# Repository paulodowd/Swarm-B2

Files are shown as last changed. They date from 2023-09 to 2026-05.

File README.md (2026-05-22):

<p align="center">
<br>
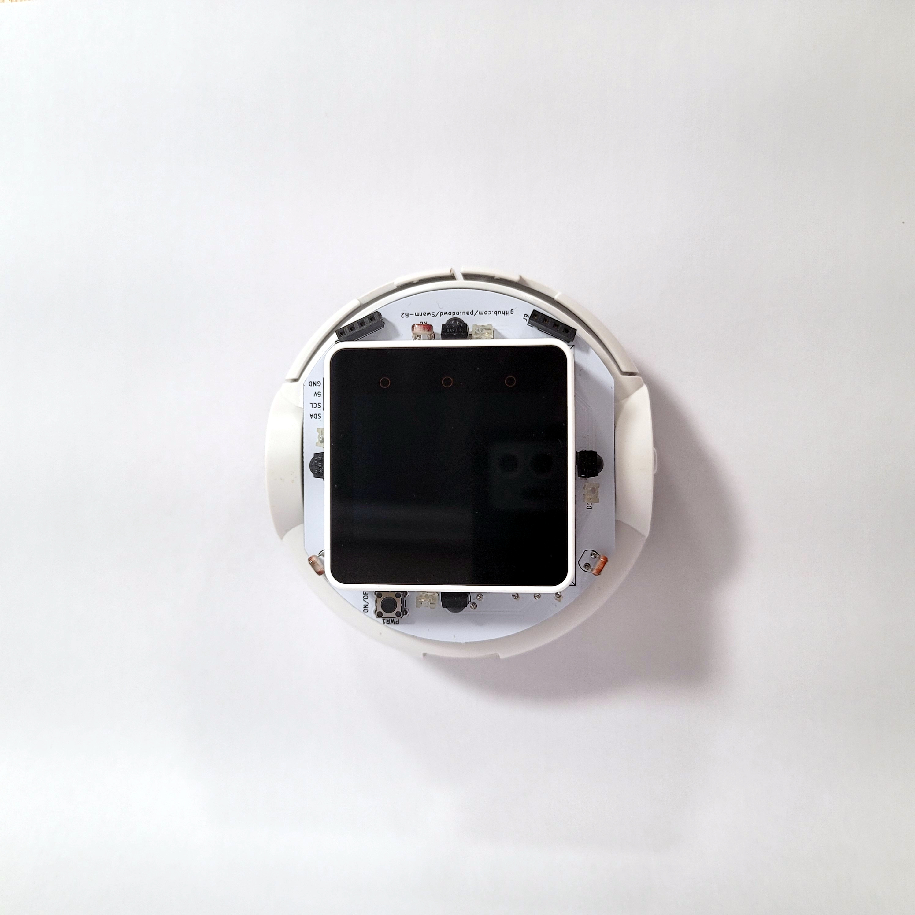
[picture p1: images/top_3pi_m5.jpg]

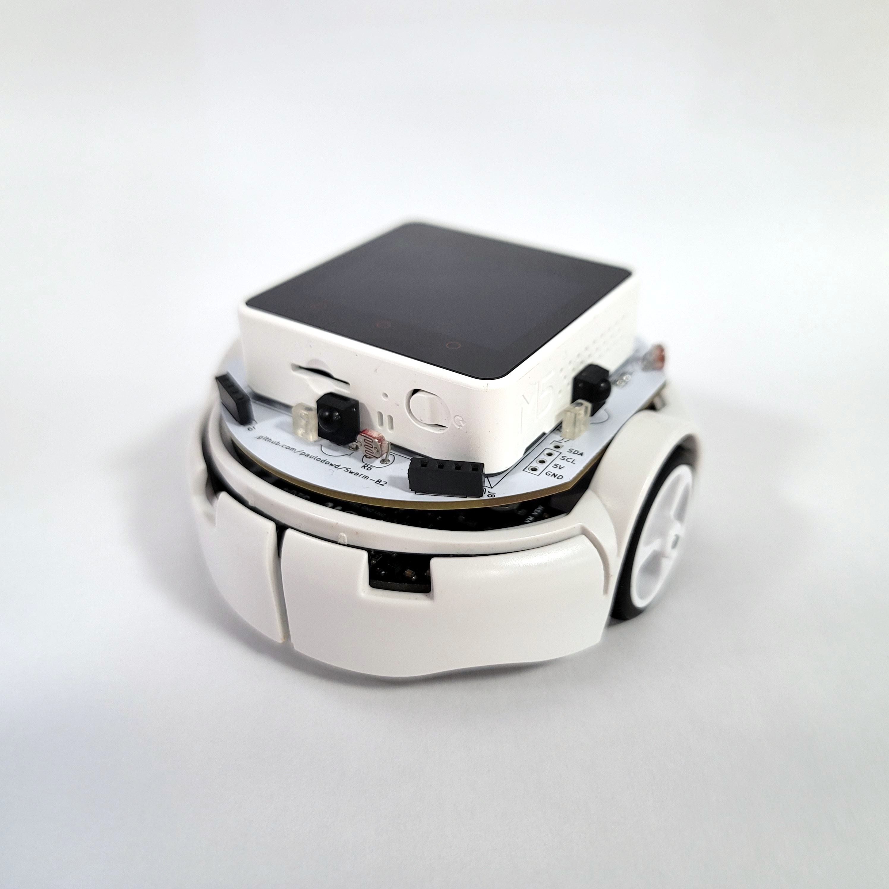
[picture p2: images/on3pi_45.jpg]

<br>
</p>

# Swarm-B2
Infra-red (IR) Communication board for Pololu 3Pi+ robots that also has a pin header to interface with an M5 Stack Core2.  This is the second major design of such a board, hence the name (S)warm (B)oard 2 - SwarmB2.  A third version is under-development with the intention to supercede this design ([SwarmB3](https://github.com/paulodowd/SwarmB3)). 

The board functions as an i2c device, so it should be relatively easy to integrate into other projects using 5v, ground, SCK and SDA connections.  The board can communicate with other SwarmB2 boards up to about 2.5m max, or down to less than a centimetre.  The firmware for the board has been written with the intention that all (or most) configuration parameters can be set at runtime, so reprogramming firmware shouldn't be necessary.

## Features
- 32 bytes per message.
- SLIP-style encoding/escaping.
- 9600 or 4800 baudrate (device dependent)
- Receive or transmit, cannot do both concurrently.
- Receiving is polled across 4 receivers.
- Transmission power set by a potentiometer (0-2.5m)
- Message framing with start delimiter and message length embedded.
- A 16 bit CRC to detect transmission errors.
- Error statistics at message level.
- Performance statitics (timings, etc).
- Bearing estimation.
- 3x LDR and 2x Sharp IR Range Finder integration on PCB.
- Reconfigurable communication strategies/priorities.
- Header pins to attach to a Pololu 3Pi+ robot.
- Header pins for an M5Stack Core2 device interfacing.

## Getting Started

The best way to get started is to download and install the example <a href="https://github.com/paulodowd/Swarm-B2/tree/main/examples/M5Visualiser">M5Visualiser</a> written for the M5Stack Core2.  This example demonstrates how to make function calls through the `SwarmB2_c` class. The class has function calls for all functionality available on the Swarm-B2, returning data types specified in the file `ircomm_i2c.h`.  

## Working with the M5Stack Core2

To get started with the M5Stack Core2, it is best to follow the manufacturers documentation to configure the Arduino IDE.  Make sure you follow the instructions for both:
- <a href="https://docs.m5stack.com/en/arduino/arduino_board">Board Management Installation</a>
- <a href="https://docs.m5stack.com/en/arduino/arduino_library">Arduino Library Installation</a>

The <a href="https://github.com/paulodowd/Swarm-B2/tree/main/examples/M5Visualiser">M5Visualiser</a> example was written against the M5Unified library - installing or using a different M5Stack library is likely to cause compilation errors for the provided example.

## Important Characteristics

### Message Size
The Swarm-B2 can receive a message of maximum length 32 bytes to transmit.  This limitation is currently defined by the Arduino i2c implementation.  The Swarm-B2 can accept a message of upto 32bytes, and it will then encode the message using a further number of bytes.   It is important to consider that when transmitting a long length message, the probability that the message will become corrupted (or similar) increases.  

### Polling
<p align="center">
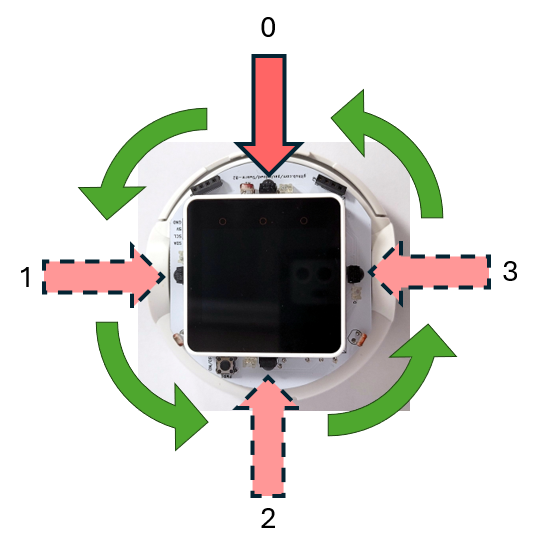
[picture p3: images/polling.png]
  
</p>
The Swarm-B2 board can only read one receiver at a time. The board is configured by default to switch which receiver is enabled as soon as one message is successfully received.  The board is also configured by default to switch receiver if it detects no activity.  Otherwise, the board is configured by default to listen for a period of time before switching receiver. 

### Transmitting
The Swarm-B2 must disable receiving to be able to transmit, otherwise it will immediately receive it's own transmission.  Therefore, the board is configured to periodically transmit messages, and in the interval period poll the receivers to receive messages.  

### Transmitting Power
The power of the IR LEDs which transmit messages can be varied via the blue potentiometer on the back of the Swarm-B2 circuit board.  The blue potentiometer has a small silver dot: rotating the white arrow indicator to point at this silver dot will produce maximum power, or maximum range of transmission.  Swarm-B2 can transmit upto 3m distance.  However, this is not very useful in a swarm/multi-robot context.  If the transmit power is set high, it is likely that the environment will become saturated with IR emissions, effectively blocking transmissions between all other robots.  The recommended position for the potentiometer is indicated in the below image with a pink dot.  This position sets the communication distance to approximately 20cm, or two robot-body lengths.

<p align="center">
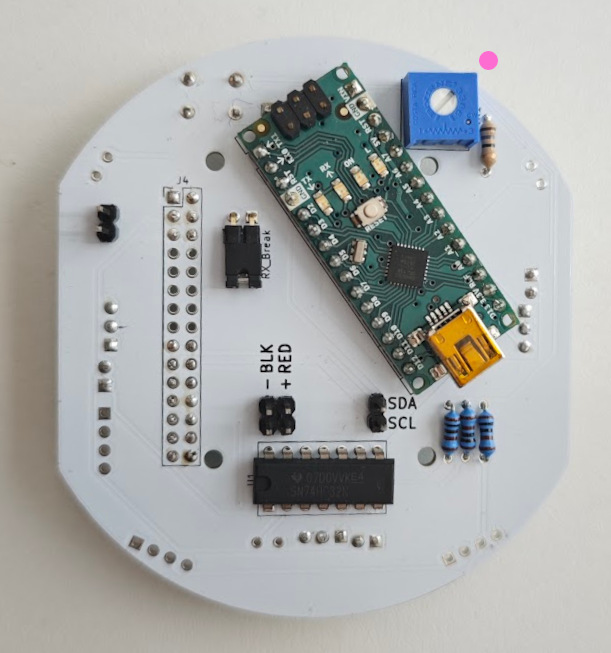
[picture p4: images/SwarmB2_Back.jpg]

</p>

### Other Configurations
It is possible to change the Swarm-B2 configuration via i2c transactions.  For example, it is possible to setup a Swarm-B2 to only transmit continously.  Or, it is possible to setup the Swarm-B2 to only receive on 1 receiver continuously.  

## FAQ

## Using the Swarm-B2 board in other Projects
This IR communication board can be used as a general purpose communication board.  The firmware on this github page is written as an i2c slave device with address `0x11`.  It should be possible to use the IR Communication board in it's current design and format with any other device that can operate the I2C protocol.  To do so, you simply need to connect the `5v`, `GND`, `SCL` and `SDA` pins appropriately to your operating device.  These physical pins are labelled on the underside of the circuit board as `+RED` (5v), `-BLK` (GND), `SDA` and `SCL`, or as `5V`, `GND`, `SCL`, `SDA` on the  topside of the circuit board.

## Fabrication, Gerber files
Navigate to folder `pcb` to find the last known gerber files sent for manufacturing, `Gerbers.zip`.  

## Schematic
The schematic of the communication board is available in picture format in the `images` folder and within the pcb folder as KiCad files.


## Interesting Information

IR communication is implemented using the standard Serial (hardware UART) functionality common to Arduino (e.g. `Serial.print()`), and so the IR circuit is electronically connected to  the Arduino TX and RX pins.  The detection (receiving) circuit uses a Demodulator chip that is tuned for a carrier frequency of 38.4Khz or 57.6Khz (more details below).  Therefore, the Arduino Nano generates a 38Khz or 58Khz signal via an internal timer interrupt to provide the transmitting carrier, output on digital pin 4.  

The carrier signal is combined electronically with the TX pin state through an OR gate (74xx32). The logic (OR) of this operation is defined by the gates sinking the current through the tranmitting IR LEDs.  Therefore, the LEDs are not driven by the 74xx32 (or the Arduino Nano, to be clear), and are considered active low.  A nice unintended side effect of this is that when TX is inactive (LOW, not transmitting), the 74xx32 output is HIGH despite the continued 38Khz signal generation - which means the IR LEDs are off and not saturating the environment.

In this circuit design, a single gate is used to sink current.  It might be important to note that the <a href="https://www.ti.com/lit/ds/symlink/sn54hc32-sp.pdf">datasheet</a> for the logic gates specifies a max current sink of 50ma through ground - and here we are potentially sinking upto 200ma from the 4 IR LEDs.    So far, I've not seen any significant changes to performance and this may be because I am not sinking current continuously, instead intermitently at 38Khz. All 4 OR gates within the 74xx32 are ganged, but the internal ground connection may still be a limitation. In either case, I haven't yet seen any problems or difference in performance.  It might be unwise to active the IR LEDs continuously (i.e. not modulated).

### Important Considerations

- **IR Demodulator:** I tried a few IR demodulator chips and they are not all created equally.  In particular, those designed to receive bursts of transmission appear poorly suited.  When using ones for burst transmission, I observed that I had to wave the transmitter or receiver around to get a successful transmission (perhaps some inner circuitry reaches a saturation?).  Instead it is better to use those designed for continuous transmission. The Vishay **TSDP34138** (<a href="https://www.farnell.com/datasheets/2245004.pdf">datasheet</a>) seems to fit this and works well / reliably.  The datasheet specifies upto 4800 baud for a 38.4Khz carrier frequency.  If you want to reproduce this board, I recommend you use the same device, or be ready for some trials of different devices.
- **Self-Receiving:** I did have an issue of a single board receiving it's own IR transmissions, and not being able to receive transmission from neighbours.  I believe this is because the UART implementation (on the Atmega328 at least) operates send (TX) and receive (RX) independently.  When using IR light, this means it will detect it's own transmission. After attempting a lot of different solutions, it was as simple as disabling the RX functionality of the UART by a register operation.  I'm glad this was available!  You can review the details of this on page 171 of the Atmega328 datasheet (<a href="https://ww1.microchip.com/downloads/en/DeviceDoc/Atmel-7810-Automotive-Microcontrollers-ATmega328P_Datasheet.pdf">here</a>).  
- **Programming the Arduino Nano:** It is important to note that the programming of the Arduino Nano will most often fail if the IR Demodulator is electronically connected.  Therefore, the circuit design has a jumper (labelled, "RX Break") intended for a connecting removable sleeve, to allow the connection to be broken for programming.  Importantly, no IR messages can be received if this jumper is not closed with the sleeve.  
- **Buffer Sizes:** The main limitation on the size of a string that can be sent over IR is actually the number of bytes that can be transferred on the I2C bus.  I think this is dependent on the Arduino Wire library and could be modifed. Or, strings to transmit could be broken into parts to transfer over I2C.  A second consideration is that the Arduino UART device has a buffer of 64 bytes.  For simplicity, the software current has buffers of 32 bytes.

## Notes on Using a M5Stack Core2

- The docs for the M5Stack Core2 are at this <a href="https://docs.m5stack.com/en/core/core2">link</a>.
- Follow the guides at <a href="https://docs.m5stack.com/en/arduino/arduino_ide">this link</a> to setup the Arduino IDE.

## Links and resources I have found useful
- Example code and discussion for different CRC algorithms: <a href="https://www.sunshine2k.de/articles/coding/crc/understanding_crc.html">link</a>
- Interesting Arduino forum post debugging CRC: <a href="https://forum.arduino.cc/t/crc-8-i2c-cyclic-redundancy-check/644812/4">link</a>
- Microchip Application Note with CRC: <a href="https://ww1.microchip.com/downloads/en/AppNotes/00730a.pdf">link</a>
- Discussion on CRC and data length: <a href="https://stackoverflow.com/questions/2321676/data-length-vs-crc-length">link</a>
- Some information on UART Baudrates: <a href="https://lucidar.me/en/serialib/most-used-baud-rates-table/">link</a>
- Discussion on start/stop bit and errors with UART: <a href="https://electronics.stackexchange.com/questions/91450/what-exactly-is-the-start-bit-error-in-uart">link</a>
- Disucssion on catching frame data overrun in UART: <a href="https://forum.arduino.cc/t/rs232-uart-frame-data-overrun-error-handling/193266/12">link</a>
- Table of ASCII values: <a href="https://www.ascii-code.com/">link</a>

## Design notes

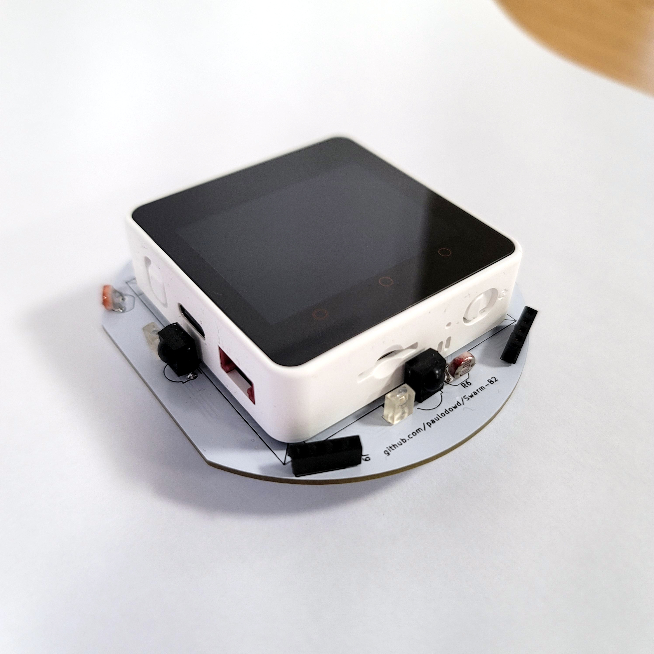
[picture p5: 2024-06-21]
images/top45_withM5.jpg

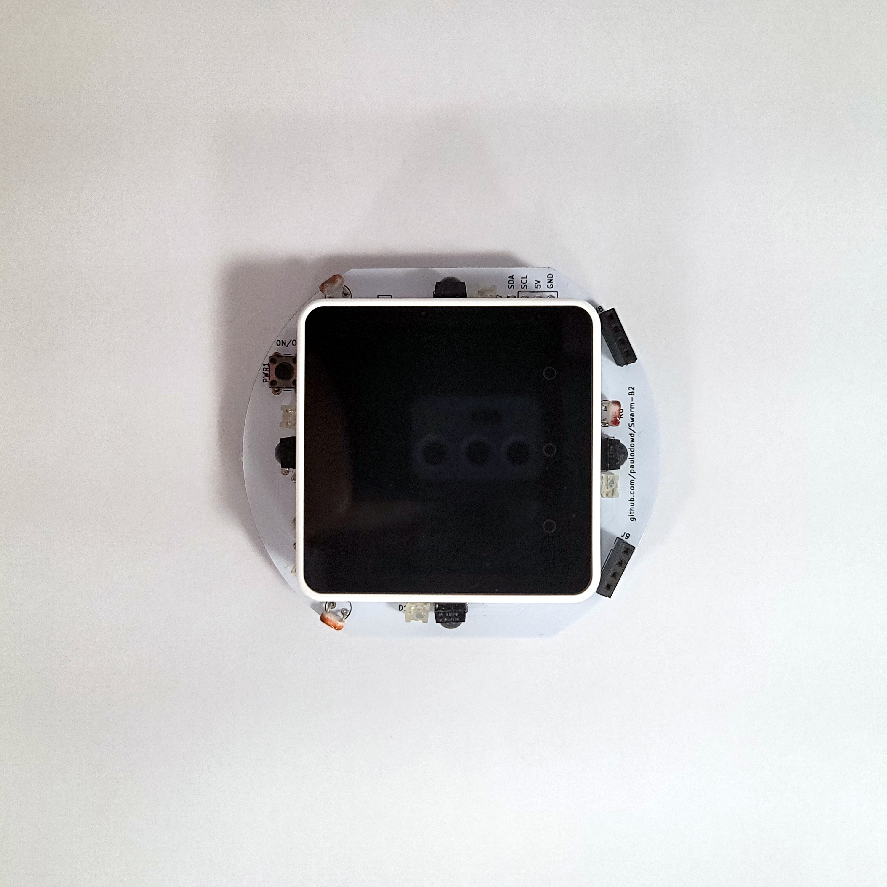
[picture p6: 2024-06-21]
images/top.jpg

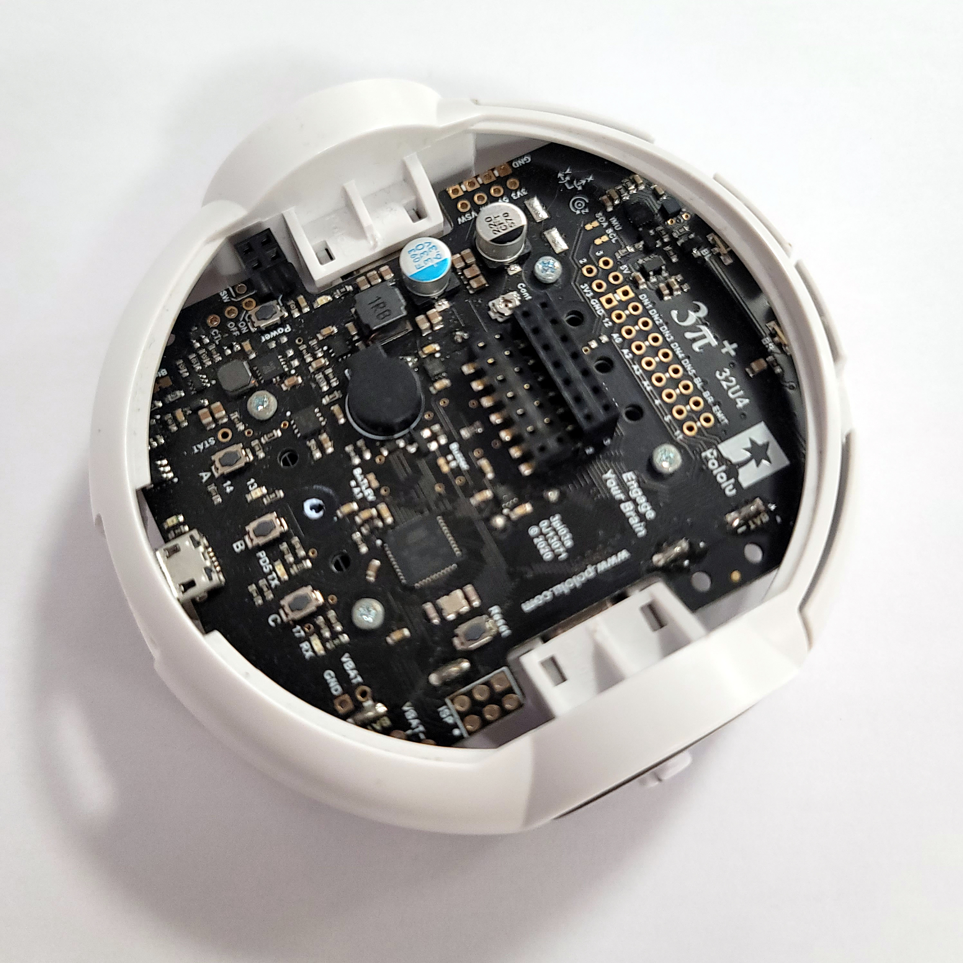
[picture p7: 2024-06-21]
images/top_3pi_modded.jpg

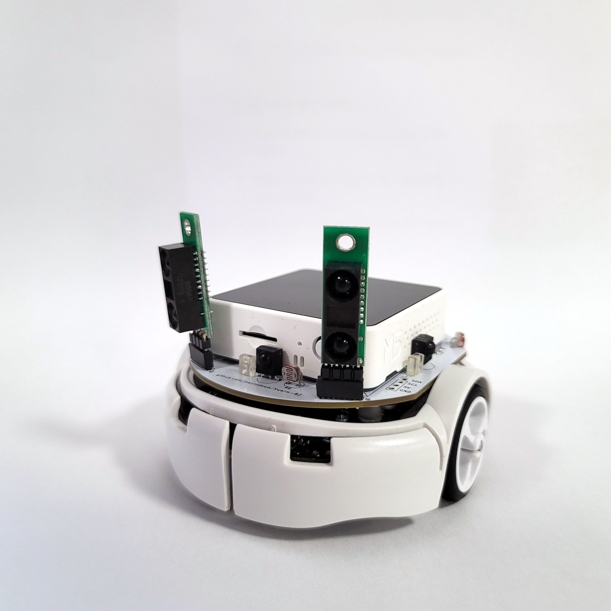
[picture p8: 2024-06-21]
images/on3pi_withProx.jpg

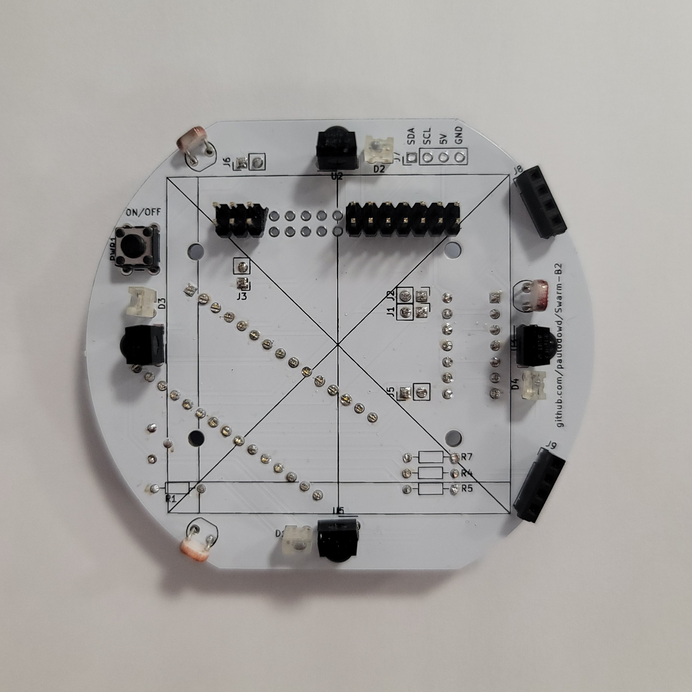
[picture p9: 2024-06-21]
images/ircomm_top.jpg

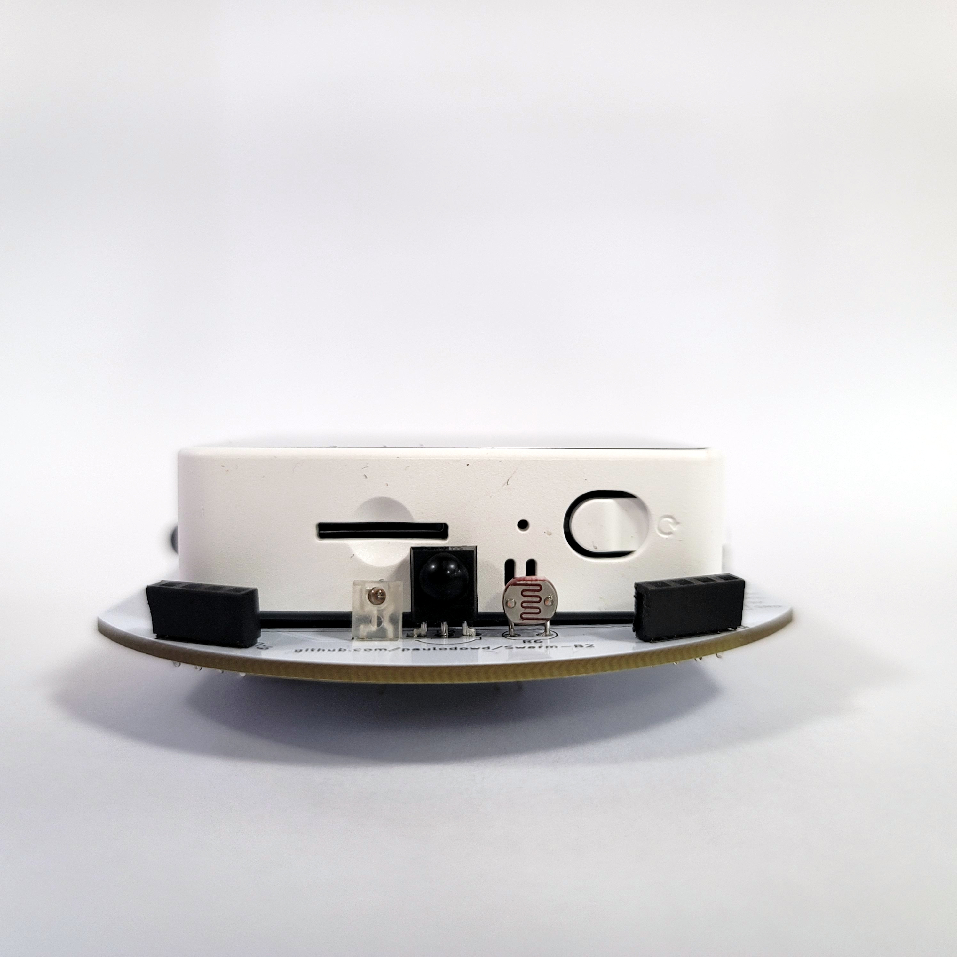
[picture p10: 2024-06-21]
images/ircomm_side_withM5.jpg

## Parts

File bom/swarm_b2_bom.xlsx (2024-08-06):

Component | Description
D1,D2,D3,D4 | IR LED, 945nm, side looking, 50 degrees emission angle
J1, J2, J5, J6 | 2 pin male header 2.54mm pitch, vertical, to Pololu 3Pi+
J3 | 2 pin male header at right angle 2.54mm pitch, for Rx_Break
J8, J9 | 4 pin female socket
J4 | M5Stack Core2 header
U1 | SN74HC32N Quad OR gate, combines UART with IR carrier signal | https://uk.farnell.com/texas-instruments/sn74hc32n/ic-quad-2-input-or-74hc32-dip14/dp/3120475 |  | 50
U2, U3, U4, U5 | TSDP34138 IR Demodulator | https://uk.farnell.com/vishay/tsdp34138/ir-receiver-35m-0-15mw-m2-side/dp/2565310 | 105 | 26.25 | 66.75
PWR1 | Mini push button 5mm
R2, R3, R6 | LDR, 5mm, 5-10k light resistance (0.5M dark resistance?).
R1 | 18R Resistor, current limiting for IR LEDs
R4, R5, R7 | 1K Resitors, potential divider for LDRs
VR1 | 1K variable resistor
A1 | Arduino Nano | https://uk.rs-online.com/web/p/arduino/6961667?searchId=df16a1f3-1ee1-491f-a64f-628fe71fe9df&gb=s |  | 58
n/a | Jumper (to connect Rx_Break)
 |  |  | 57

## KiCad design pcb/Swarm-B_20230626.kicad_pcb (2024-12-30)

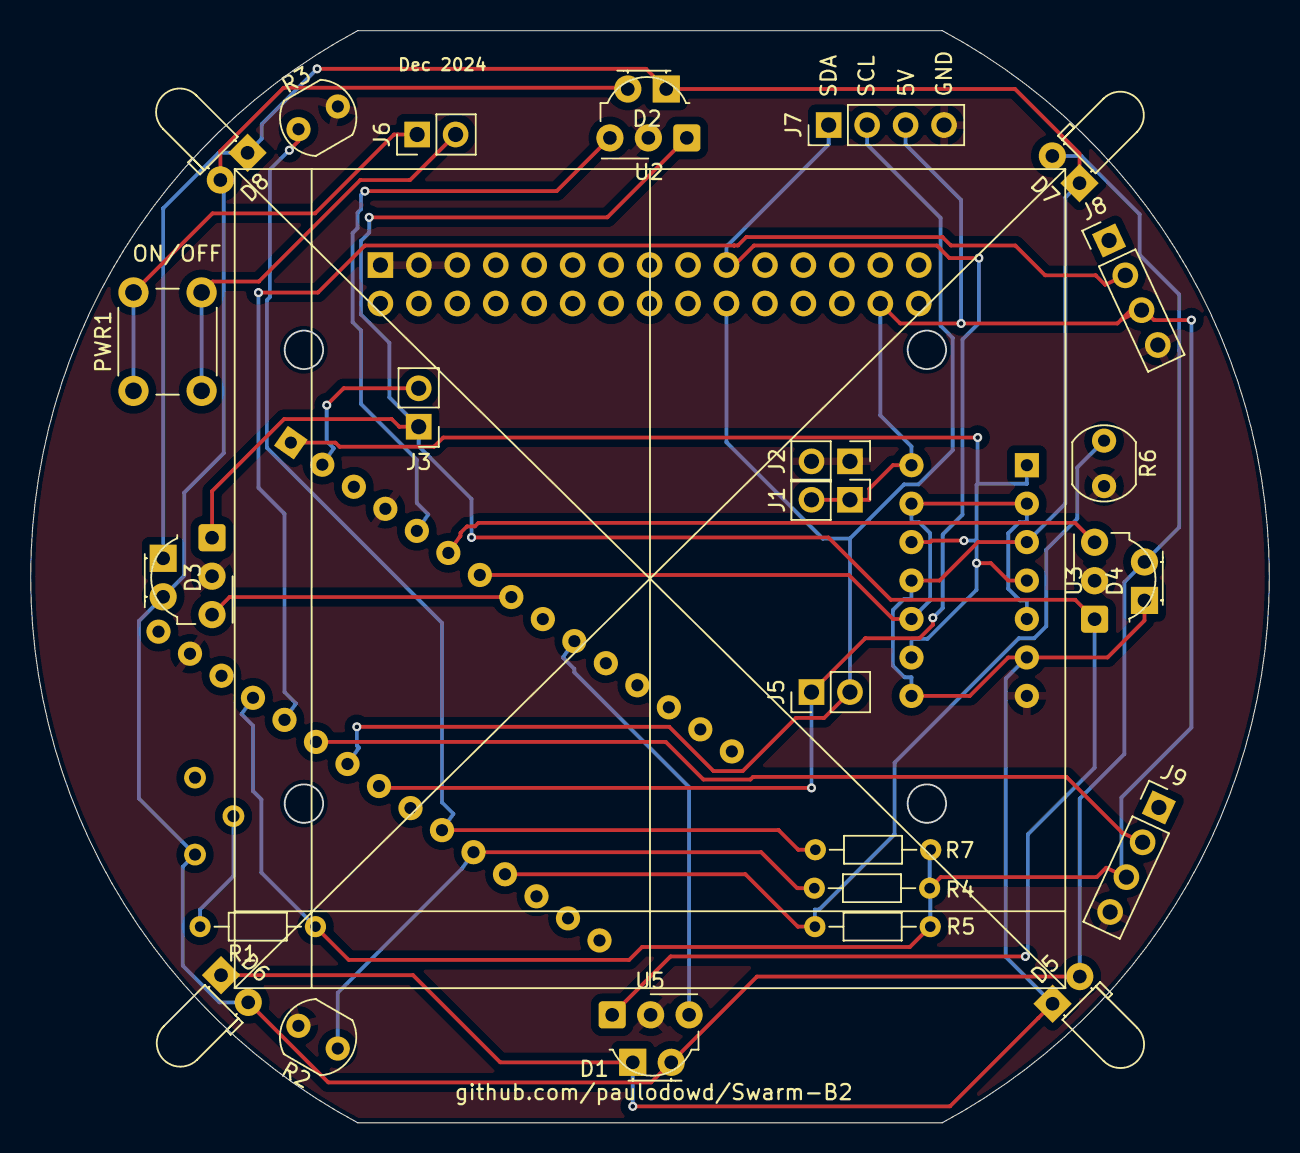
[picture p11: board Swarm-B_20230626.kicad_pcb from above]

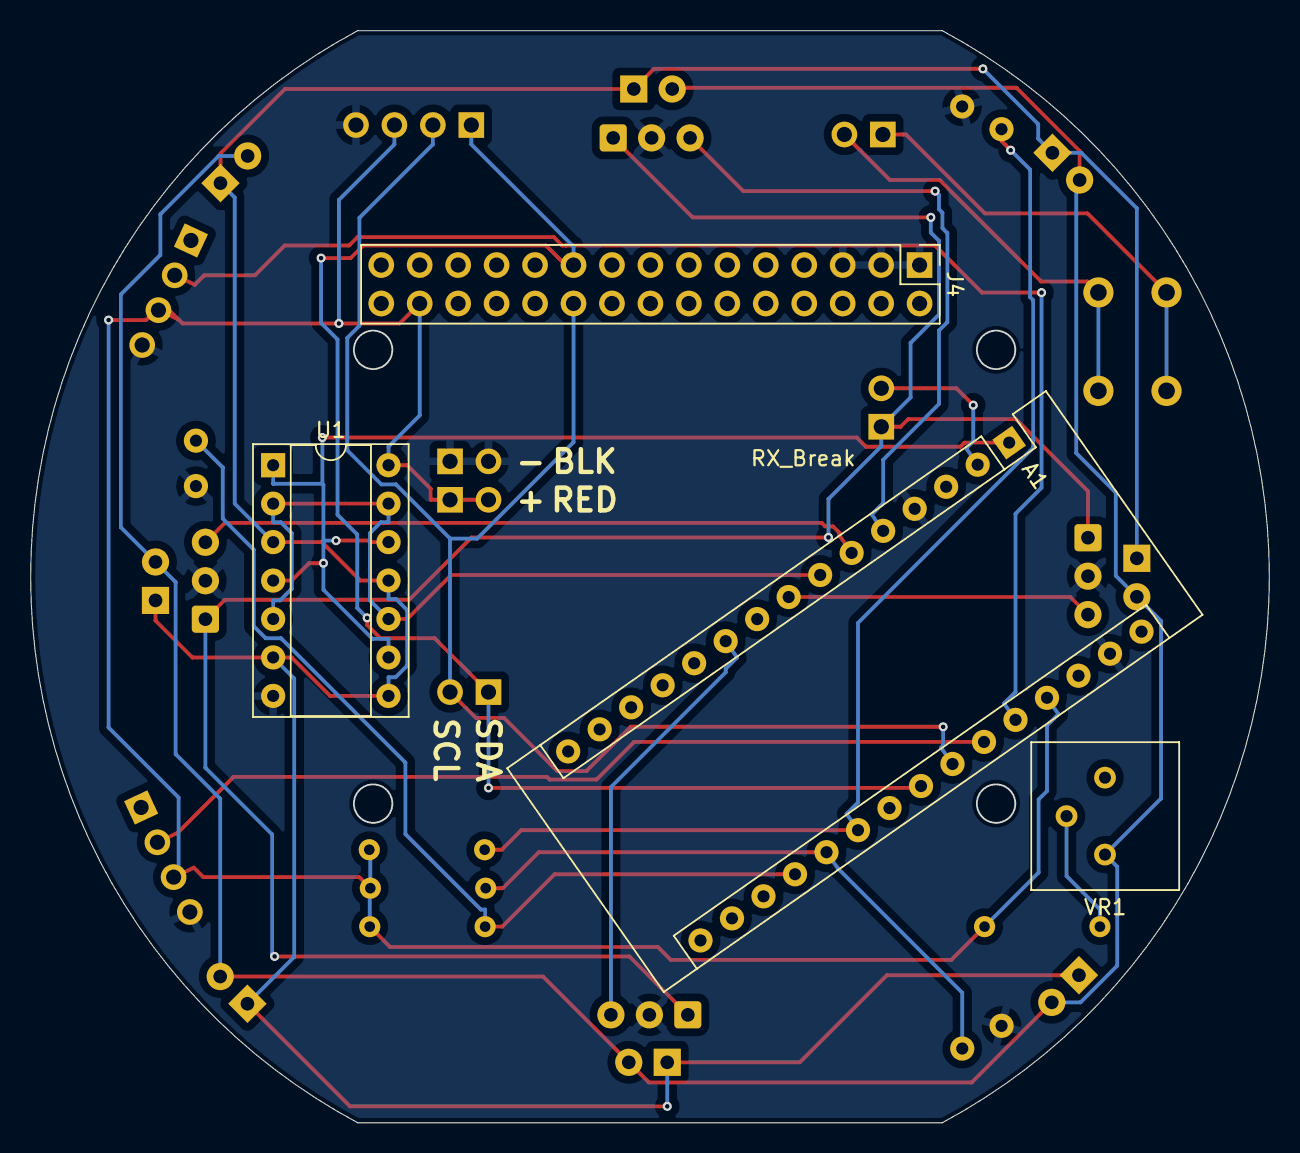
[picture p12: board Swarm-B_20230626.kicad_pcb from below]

Board: 2 copper layers, 81.8 x 72.1 mm, 32 parts (4 on the bottom side), 22 nets.

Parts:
A1: Arduino_Nano_v3.x; Arduino_Nano
D1, D2, D3, D4, D5, D6, D7, D8: IR_LED; LED_D3.0mm_Horizontal_O1.27mm_Z2.0mm
J1: 5v_3Pi; PinHeader_1x02_P2.54mm_Vertical
J2: GND_3Pi; PinHeader_1x02_P2.54mm_Vertical
J3: RX_Break; PinHeader_1x02_P2.54mm_Vertical
J4: Conn_02x15_Top_Bottom; PinHeader_2x15_P2.54mm_Vertical
J5: I2C_3Pi; PinHeader_1x02_P2.54mm_Vertical
J6: 3PI_SWTCH; PinHeader_1x02_P2.54mm_Vertical
J7: I2C_Exp; PinHeader_1x04_P2.54mm_Vertical
J8: ProxA; PinHeader_1x04_P2.54mm_Vertical
J9: ProxB; PinHeader_1x04_P2.54mm_Vertical
PWR1: Bttn; SW_PUSH_6mm
R1: 15R_IRLED; R_Axial_DIN0204_L3.6mm_D1.6mm_P7.62mm_Horizontal
R2, R3, R6: LDR; R_LDR_5.0x4.1mm_P3mm_Vertical
R4, R5, R7: 10K_LDR; R_Axial_DIN0204_L3.6mm_D1.6mm_P7.62mm_Horizontal
U1: 74LS32; DIP-14_W7.62mm_Socket
U2, U3, U4, U5: TSDP34138; Vishay_MOLD-3Pin
VR1: 1K_Pot_IRLED; Potentiometer_Bourns_3386P_Vertical

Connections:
+5V: A1.27 (+5V), J1.1, J1.2, J4.28, J7.3, J8.3, J9.3, R1.1, R4.1, R5.1, R7.1, U1.14 (VCC)
GND: A1.4 (GND), A1.29 (GND), J2.1, J2.2, J4.1, J4.3, J4.5, J7.4, J8.4, J9.4, R2.2, R3.2, R6.2, U1.7 (GND), U2.2 (GND), U3.2 (GND), U4.2 (GND), U5.2 (GND)
unnamed: A1.19 (A0), R5.2, R6.1
unnamed: A1.20 (A1), R2.1, R4.2
unnamed: A1.21 (A2), R3.1, R7.2
unnamed: A1.23 (A4), J4.19, J5.1, J7.1
unnamed: A1.24 (A5), J4.20, J5.2, J7.2
unnamed: A1.25 (A6), J9.2
unnamed: A1.26 (A7), J8.2
unnamed: A1.2 (D0/RX), J3.2
unnamed: A1.1 (D1/TX), U1.1, U1.4, U1.9, U1.12
unnamed: A1.5 (D2), U2.3 (Vs)
unnamed: A1.6 (D3), U3.3 (Vs)
unnamed: A1.7 (D4), U1.2, U1.5, U1.10, U1.13
unnamed: A1.8 (D5), U4.3 (Vs)
unnamed: A1.10 (D7), U5.3 (Vs)
unnamed: D1.2 (A), D2.2 (A), D3.2 (A), D4.2 (A), D5.2 (A), D6.2 (A), D7.2 (A), D8.2 (A), VR1.3 (CW)
unnamed: D1.1 (K), D2.1 (K), D3.1 (K), D4.1 (K), D5.1 (K), D6.1 (K), D7.1 (K), D8.1 (K), U1.3, U1.6, U1.8, U1.11
unnamed: J6.1, PWR1.1
unnamed: J6.2, PWR1.2
unnamed: J3.1, U2.1 (OUT), U3.1 (OUT), U4.1 (OUT), U5.1 (OUT)
unnamed: R1.2, VR1.2 (WIPER)

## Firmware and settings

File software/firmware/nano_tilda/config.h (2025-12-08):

// The following provide the default configuration
// of the communication board.

#ifndef IRCOMM_CONFIG_H
#define IRCOMM_CONFIG_H




// Uncomment depending on your IR
// Receiver module.  This will determine
// the correct Serial Baud rate and the
// configuration of timer2 for the carrier
// signal
// Other parts of the code depend on this
// being set correctly.
//#define IR_FREQ_38  // For chip TSDP34138
#define IR_FREQ_58    // For chip TSDP34156

// If we know we are going to send and receive
// messages of a certain length then we could
// configure the device for a more optimal
// rx_delay and tx_delay.  To try and have the
// board do this for itself, set the below to
// true.  Set true, the board will look at the
// length of the message to transmit and the
// length of messages received, and setup the
// tx_delay and rx_delay to be appropriate for
// which ever of the two is longest.
// If set to false, the board will use the
// #defines set above for tx/rx_delay _bias _mod.
#define RX_CYCLE              false  // should the board poll receivers?
#define RX_CYCLE_ON_RX        false  // if a message is received, cycle?
#define RX_PREDICT_PERIOD    false  // try to optimse polling performance?
#define RX_PREDICT_MULTIPLIER 1.0   // how many message-size to wait?
#define RX_DESYNC             false
#define RX_DESATURATE         false
#define RX_OVERRUN            true  // allow for rx message to complete? 
#define RX_DEFAULT_MSG_LEN    MAX_MSG // 36 is worst case
#define RX_SKIP_MULTI         4
#define RX_RAND_RX            false
#define RX_SKIP_INACTIVE      true
#define MS_PER_BYTE_58KHZ     1.2   // 58khz
#define MS_PER_BYTE_38KHZ     2.5   // 38khz
#define US_PER_BYTE_58KHZ     1250   // 58khz
#define US_PER_BYTE_38KHZ     2500   // 38khz

// A rough estimate of how many ms per byte 
// during the transmit/receive process.
#ifdef IR_FREQ_58
#define RX_BYTE_TIMEOUT_MS       (MS_PER_BYTE_58KHZ*4)
#endif
#ifdef IR_FREQ_38
#define RX_BYTE_TIMEOUT_MS       (MS_PER_BYTE_38KHZ*4)     
#endif

#ifdef IR_FREQ_58
#define RX_PERIOD_MAX       (MS_PER_BYTE_58KHZ*RX_DEFAULT_MSG_LEN)     
#endif
#ifdef IR_FREQ_38
#define RX_PERIOD_MAX       (MS_PER_BYTE_38KHZ*RX_DEFAULT_MSG_LEN)     
#endif

#ifdef IR_FREQ_58
#define RX_SAT_TIMEOUT_US       (20000) // I measured 8000us for ambient noise
#endif
#ifdef IR_FREQ_38
#define RX_SAT_TIMEOUT_US       (20000)     
#endif




// What system should we use for the tranmission?
// Periodic: Decouples receiving from transmission, meaning
//          that tranmission happens every (x)ms.
// Interleaved: Means that after a receiver is rotated, we
//          also transmit.  This means that if a robot is
//          receiving messages well, the tranmission rate
//          would also increase.  Seems complicated.
#define TX_MODE_PERIODIC     0 // tx periodically, timing set below
#define TX_MODE_INTERLEAVED  1 // tx after every receiver rotation (not working)
#define TX_MODE (TX_MODE_PERIODIC)
//#define TX_MODE (TX_MODE_INTERLEAVED)
#define TX_PREDICT_PERIOD     true
#define TX_PREDICT_MULTI      4.0
#define TX_PREAMBLE           true
#define TX_PREAMBLE_REPEAT    4
#define TX_PREAMBLE_BYTE      0x55 // 0b01010101

// When set in TX_MODE_PERIODIC
// How long should the robot wait before doing another
// transmission?  
// For 38khz, a 32byte message will take approximately 
// 80ms to transmit/receive.
// For 58khz, a 32byte message will take approximately 
// 39ms to transmit/receive
#ifdef IR_FREQ_38
#define DEFAULT_TX_PERIOD (320) // in ms, 0 disables tx
#endif

#ifdef IR_FREQ_58
#define DEFAULT_TX_PERIOD (160) // in ms, 0 disables tx
#endif

// Should we try to break synchrony between robots
// by randomising the tx period?
#define TX_DESYNC  1

 // Try to minimise interference by only transmitting
 // when no other IR transmission has been detected
 // If IR detected, will try again on next iteration
#define TX_DEFER   0

// How many times should we repeat the transmission
// of a message? This should be set as a positive
// no zero value (1+)
#define DEFAULT_TX_REPEAT 3



// How often should the bearing estimate be updated?
#define UPDATE_BEARING_MS  250


// I2C constrains the message payload to 32
// bytes.  
#define MAX_MSG 32

// When we encode a message, the worst case
// is 32 bytes of payload, and each byte is
// escaped with a byte. We also need to add
// the start, length and CRC bytes (+4).
#define MAX_TX_BUF (MAX_MSG * 2) + 4



#define RX_PWR_0  3 // Forward
#define RX_PWR_1  2 // LEFT
#define RX_PWR_2  5 // BACK
#define RX_PWR_3  7 // RIGHT
#define MAX_RX  4 // How many?


// 38Khz signal generated on
// digital pin 4.
#define TX_CLK_OUT 4



#endif

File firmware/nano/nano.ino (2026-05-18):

#include <avr/io.h>
#include <Wire.h>
#include "ircomm.h"
#include "ircomm_i2c.h"

// Pin definitions for extra sensors
// on the communication board, if present
#define LDR0_PIN  A0
#define LDR1_PIN  A1
#define LDR2_PIN  A2
#define PROX0_PIN A6
#define PROX1_PIN A7

// Used to control the IR communication.
IRComm_c ircomm;

volatile boolean full_reset;

volatile ir_mode_t last_mode;

// Function to receive commands from the master device.
// This will typically be in the format of a mode change
// and then any appropriate data.
void i2c_receive( int len ) {


  // Mode changes are always 1 byte long.  We use these to
  // ready the board to send back information or to ask the
  // board to complete specific actions (e.g, delete a
  // message).
  // It is possible to send a 1 byte message, so we catch
  // that possibility here.  The other time we may set
  // data is for rx and tx settings, but these will
  // always be len > 1c
  if ( len == 1 && last_mode.mode != MODE_SET_MSG ) { // receiving a mode change.
    ir_mode_t new_mode;
    Wire.readBytes( (byte*)&new_mode, sizeof( new_mode ) );


    // Check we are setting to a valid mode.
    // Data type cannot represent negative
    if ( new_mode.mode < MAX_MODE ) {
      last_mode.mode = new_mode.mode;
    }

    // For instant mode changes
    // Should we set a last_mode state after this?
    if ( new_mode.mode == MODE_STOP_TX ) {

      // Clearing tx  buff will stop transmission of messages
      ircomm.clearTxBuf();

      
    } else if ( new_mode.mode == MODE_RESET_METRICS ) {
      ircomm.resetMetrics();
    } else if ( new_mode.mode == MODE_FULL_RESET ) {
      full_reset = true;
    } else if ( new_mode.mode == MODE_STOP_RX ) {
      ircomm.disabled = true;

    } else if ( new_mode.mode == MODE_START_RX ) {

      ircomm.disabled = false;

    } else if ( new_mode.mode == MODE_CLEAR_MSG0 ) {
      // Delete message
      ircomm.clearRxMsg( 0 );

    } else if ( new_mode.mode == MODE_CLEAR_MSG1 ) {
      // Delete message
      ircomm.clearRxMsg( 1 );

    } else if ( new_mode.mode == MODE_CLEAR_MSG2 ) {
      // Delete message
      ircomm.clearRxMsg( 2 );

    } else if ( new_mode.mode == MODE_CLEAR_MSG3 ) {
      // Delete message
      ircomm.clearRxMsg( 3 );


    } else if ( new_mode.mode == MODE_CLEAR_HIST ) {
      //      ircomm.hist[0] = 0;
      //      ircomm.hist[1] = 0;
      //      ircomm.hist[2] = 0;
      //      ircomm.hist[3] = 0;
    } else if ( new_mode.mode == MODE_SET_MSG ) {
      last_mode.mode = MODE_SET_MSG;
    }

  } else if ( last_mode.mode == MODE_SET_MSG ) {

    // This should be impossible...
    if ( len > MAX_MSG || len < 1 ) {
      //ircomm.clearTxBuf();
      // clear i2c buffer
      while ( Wire.available() ) Wire.read();
    } else {

      // Transfer bytes, encode with parser
      byte buf[MAX_MSG];
      memset( buf, 0, sizeof( buf ));
      Wire.readBytes( buf, len );
      ircomm.config.tx.len = ircomm.parser.formatIRMessage( (uint8_t*)ircomm.tx_buf, buf, len );
    }

    last_mode.mode = MODE_NOT_SET;

  } else if ( last_mode.mode == MODE_SET_RX ) {

    if ( len == sizeof( ir_rx_params_t ) ) {

      Wire.readBytes( (uint8_t*)&ircomm.config.rx, sizeof( ircomm.config.rx ));

      // User may have switched Rx index!
      // This also resets the parser & UART
      ircomm.powerOnRx( ircomm.config.rx.index );

    } else {

      // Something has gone wrong. Just
      // read in the bytes to clear the
      // data
      while ( Wire.available() ) Wire.read();
    }
    last_mode.mode = MODE_NOT_SET;

  } else if ( last_mode.mode == MODE_SET_TX ) {
    if ( len == sizeof( ir_tx_params_t ) ) {
      Wire.readBytes( (uint8_t*)&ircomm.config.tx, sizeof( ircomm.config.tx ));

      
    } else {

      // Something has gone wrong. Just
      // read in the bytes to clear the
      // data
      while ( Wire.available() ) Wire.read();
    }

    last_mode.mode = MODE_NOT_SET;

  } else {

    // Unhandled
  }

}

// When the 3Pi or Core2 calls an i2c request, this function
// is executed.
void i2c_request() {

  if ( last_mode.mode == MODE_REPORT_STATUS ) {
    Wire.write( (byte*)&ircomm.ir_status, sizeof(ircomm.ir_status) );

  } else if ( last_mode.mode == MODE_REPORT_CRC ) {

    Wire.write( (byte*)&ircomm.metrics.crc, sizeof(ircomm.metrics.crc) );

  } else if ( last_mode.mode == MODE_REPORT_ACTIVITY ) {

    Wire.write( (byte*)&ircomm.metrics.activity, sizeof(ircomm.metrics.activity) );

  } else if ( last_mode.mode == MODE_REPORT_SATURATION ) {

    Wire.write( (byte*)&ircomm.metrics.saturation, sizeof(ircomm.metrics.saturation) );

  } else if ( last_mode.mode == MODE_REPORT_SKIPS ) {

    Wire.write( (byte*)&ircomm.metrics.skips, sizeof(ircomm.metrics.skips) );

  } else if ( last_mode.mode == MODE_REPORT_MSG_TIMINGS ) {

    Wire.write( (byte*)&ircomm.metrics.msg_timings, sizeof( ircomm.metrics.msg_timings ) );

  }  else if ( last_mode.mode == MODE_REPORT_BYTE_TIMINGS ) {

    Wire.write( (byte*)&ircomm.metrics.byte_timings, sizeof( ircomm.metrics.byte_timings ) );

  }  else if ( last_mode.mode == MODE_REPORT_LEN_MSG0) {

    ir_msg_len_t msg_len;
    msg_len.n_bytes = ircomm.msg_len[0];
    Wire.write( (byte*)&msg_len, sizeof( msg_len ) );


  } else if ( last_mode.mode == MODE_REPORT_LEN_MSG1 ) {
    
    ir_msg_len_t msg_len;
    msg_len.n_bytes = ircomm.msg_len[1];
    Wire.write( (byte*)&msg_len, sizeof( msg_len ) );


  } else if ( last_mode.mode == MODE_REPORT_LEN_MSG2 ) {
    
    ir_msg_len_t msg_len;
    msg_len.n_bytes = ircomm.msg_len[2];
    Wire.write( (byte*)&msg_len, sizeof( msg_len ) );


  } else if ( last_mode.mode == MODE_REPORT_LEN_MSG3 ) {

    ir_msg_len_t msg_len;
    msg_len.n_bytes = ircomm.msg_len[3];
    Wire.write( (byte*)&msg_len, sizeof( msg_len ) );

  } else if ( last_mode.mode == MODE_REPORT_MSG0 ) {
    if ( ircomm.msg_len[0] == 0 ) {
      Wire.write("!");  // Error token
    } else {
      Wire.write( ircomm.ir_msg[0], ircomm.msg_len[0] );
      // Delete message
      ircomm.clearRxMsg( 0 );
    }

  } else if ( last_mode.mode == MODE_REPORT_MSG1 ) {
    if ( ircomm.msg_len[1] == 0 ) {
      Wire.write("!");
    } else {
      Wire.write( ircomm.ir_msg[1], ircomm.msg_len[1] );
      // Delete message
      ircomm.clearRxMsg( 1 );
    }

  } else if ( last_mode.mode == MODE_REPORT_MSG2 ) {
    if ( ircomm.msg_len[2] == 0 ) {
      Wire.write("!");
    } else {
      Wire.write( ircomm.ir_msg[2], ircomm.msg_len[2] );

      // Delete message
      ircomm.clearRxMsg( 2 );
    }


  } else if ( last_mode.mode == MODE_REPORT_MSG3 ) {
    if ( ircomm.msg_len[3] == 0 ) {
      Wire.write("!");
    } else {
      Wire.write( ircomm.ir_msg[3], ircomm.msg_len[3] );

      // Delete message
      ircomm.clearRxMsg( 3 );
    }

  } else if ( last_mode.mode == MODE_REPORT_CYCLES ) {

    // Transmit
    Wire.write( (byte*)&ircomm.metrics.cycles, sizeof( ircomm.metrics.cycles ) );

  } else if ( last_mode.mode == MODE_REPORT_ERRORS ) {

    // Transmit
    Wire.write( (byte*)&ircomm.metrics.errors, sizeof( ircomm.metrics.errors ) );

  } else if ( last_mode.mode == MODE_REPORT_RX_VECTORS ) {

    // Transmit
    Wire.write( (byte*)&ircomm.metrics.vectors, sizeof( ircomm.metrics.vectors) );

  } else if (  last_mode.mode == MODE_REPORT_RX_BEARING ) {

    // Transmit
    Wire.write( (byte*)&ircomm.metrics.bearing, sizeof( ircomm.metrics.bearing ) );

  } else if ( last_mode.mode == MODE_REPORT_SENSORS ) {

    // Collect sensor readings - should be very quick
    ircomm.metrics.sensors.ldr[0] = (int16_t)analogRead( LDR0_PIN );
    ircomm.metrics.sensors.ldr[1] = (int16_t)analogRead( LDR1_PIN );
    ircomm.metrics.sensors.ldr[2] = (int16_t)analogRead( LDR2_PIN );
    ircomm.metrics.sensors.prox[0] = (int16_t)analogRead( PROX0_PIN );
    ircomm.metrics.sensors.prox[1] = (int16_t)analogRead( PROX1_PIN );

    // Transmit
    Wire.write( (byte*)&ircomm.metrics.sensors, sizeof( ircomm.metrics.sensors ) );

  } else if ( last_mode.mode == MODE_REPORT_HIST ) {

    Wire.write( (byte*)&ircomm.metrics.hist, sizeof( ircomm.metrics.hist ) );

  } else if ( last_mode.mode == MODE_GET_TX ) {

    Wire.write( (byte*)&ircomm.config.tx, sizeof( ircomm.config.tx ) );


  } else if ( last_mode.mode == MODE_GET_RX ) {

    Wire.write( (byte*)&ircomm.config.rx, sizeof( ircomm.config.rx ) );

  }

}


void setup() {

  // Set random seed.
  initRandomSeed();

  // Pinmodes for LDR
  pinMode(LDR0_PIN, INPUT);
  pinMode(LDR1_PIN, INPUT);
  pinMode(LDR2_PIN, INPUT);
  pinMode(PROX0_PIN, INPUT);
  pinMode(PROX1_PIN, INPUT);

  // Debug LED
  pinMode( 13, OUTPUT );

  // Begin I2C as a slave device.
  Wire.begin( IRCOMM_I2C_ADDR );
  Wire.onReceive( i2c_receive );
  Wire.onRequest( i2c_request );

  // Start the IR communication board.
  ircomm.init();


  last_mode.mode = MODE_NOT_SET;

  full_reset = false;


  // Paul: I was using this to test
//  setRandomMsg(8);
}




// Construct a message of length len out
// of random ascii characters, avoiding
// * and @
int setRandomMsg(int len) {
  // Let's test variable message lengths
  char buf[ MAX_MSG ];


  memset( buf, 0, sizeof( buf ) );

  //sprintf( buf, "%lu", millis() );
  //int ms_len = strlen( buf );
  //buf[ms_len] = ':';
  //ms_len++;

  sprintf(buf, "paul_test");
  len = 9;
  //    sprintf(buf, "12345678");
  
  // Create a random test string, but exclude our
  // token characters
//  for ( int i = 0; i < len; i++ ) {
//    do {
//      buf[i] = (char)random( 0, 256 );
//    } while( buf[i] == '~' || buf[i] == '^' );
//  }

  //  typedef struct msg {
  //    float v[2];
  //  } msg_t;
  //  msg_t msg;
  //  for ( int i = 0; i < 2; i++ ) msg.v[i] = random(0, 1000) - 500;
  //  ircomm.tx_len = ircomm.parser.formatIRMessage( ircomm.tx_buf, (byte*)&msg, sizeof( msg ) );


  //  Checking the format of what is being sent.
  ircomm.config.tx.len = ircomm.parser.formatIRMessage( (uint8_t*)ircomm.tx_buf, (uint8_t*)buf, len );
  //  while(1) {
  //    Serial.print("tx buf: ");
  //    Serial.println( (char*)ircomm.tx_buf );
  //    for( int i = 0; i < ircomm.tx_len; i++ ) {
  //      Serial.print( (char)ircomm.tx_buf[i] );
  //      Serial.print( " = " );
  //      Serial.print( ircomm.tx_buf[i], DEC);
  //      Serial.print(",");
  //    }
  //    Serial.println();
  //    delay(1000);
  //
  //  }

  //  while (true) {
  //    ircomm.printMsgForDebugging();
  //
  //    delay(500);
  //  }


  return ircomm.config.tx.len;
}

void loop() {
  ////
//    ircomm.doTransmit();
//    return;


  if ( full_reset ) {
    ircomm.fullReset();
    full_reset = false;
  }


  // This line must be called to process new
  // received messages and transmit new messages
  ircomm.update();
}



// Experiment to see if reading the LSB
// of an analog read can generate a
// useful random seed.  Nothing connected
// to A3, so it is floating and picking up
// emf.
void initRandomSeed() {
  pinMode(A3, INPUT);
  byte r = 0x00;
  for ( int i = 0; i < 8; i++ ) {
    byte b = (byte)analogRead(A3);
    b = b & 0x01;
    //Serial.println(b, BIN);

    r |= (b << i);
    delayMicroseconds(10);
  }
  //Serial.println(r, BIN);
  randomSeed( r );
}

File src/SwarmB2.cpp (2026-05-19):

#include "SwarmB2.h"
#include <Wire.h>
#include <stdint.h>
#include <limits.h>

void SwarmB2_c::init() {
  memset( (void*)&rx_settings, 0, sizeof( rx_settings ));
  memset( (void*)&tx_settings, 0, sizeof( tx_settings ));

  // Populate the board config cache ready for
  // any subsequent user changes
  getRxSettings();
  delay(5);
  getTxSettings();
  delay(5);

  // Ensure we have default settings
  configureDefault();
}


void SwarmB2_c::configureDefault() {

  // Settings for receiving
  rx_settings.flags.bits.cycle_on_rx    = true;
  rx_settings.flags.bits.desync         = true;
  rx_settings.flags.bits.overrun        = true;
  rx_settings.flags.bits.rand_rx        = false;
  rx_settings.flags.bits.rx0            = true;
  rx_settings.flags.bits.rx1            = true;
  rx_settings.flags.bits.rx2            = true;
  rx_settings.flags.bits.rx3            = true;
  rx_settings.skip_multi                = 0;
  rx_settings.predict_multi             = 0;
  rx_settings.index                     = 0;
  rx_settings.period_base_ms            = 60;
  rx_settings.timeout_multi             = 0;
  rx_settings.saturation_us             = 20000;
  setRxSettings();

  // Settings for tranmission
  tx_settings.flags.bits.desync = 1;
  tx_settings.repeat            = 3;
  tx_settings.predict_multi     = 4;
  tx_settings.defer_multi       = 1;
  tx_settings.preamble_repeat   = 4;
  tx_settings.period_base_ms    = 170;
  setTxSettings();

  resetMetrics();
}

void SwarmB2_c::updateSettings() {

  // Settings for receiving
  rx_settings.flags.bits.cycle_on_rx    = true;
  rx_settings.flags.bits.desync         = false;
  rx_settings.flags.bits.overrun        = true;
  rx_settings.flags.bits.rand_rx        = false;
  rx_settings.flags.bits.rx0            = true;
  rx_settings.flags.bits.rx1            = true;
  rx_settings.flags.bits.rx2            = true;
  rx_settings.flags.bits.rx3            = true;
  rx_settings.skip_multi                = 0;
  rx_settings.predict_multi             = 4;
  rx_settings.index                     = 0;
  rx_settings.period_base_ms            = 60;
  rx_settings.timeout_multi             = 6;
  rx_settings.saturation_us             = 20000;
  setRxSettings();

  // Settings for tranmission
  tx_settings.flags.bits.desync = 1;
  tx_settings.repeat            = 3;
  tx_settings.predict_multi     = 4;
  tx_settings.defer_multi       = 0;
  tx_settings.preamble_repeat   = 4;
  tx_settings.period_base_ms    = 170;
  setTxSettings();

  resetMetrics();
}


// This function is used to fetch a message
// from one of the four receivers on the
// IR communication board. This function will
// complete the check of whether or not there
// is a message available.
// Return:
//  -1    invalid request
//   0    no message available
//  [1:32]valid message length
int SwarmB2_c::getIRMessage( uint8_t * buf, int which_rx ) {

  // Bad request
  if ( which_rx < 0 || which_rx > 3 ) return -1;

  // Get the message status from the board (1 byte)
  ir_status_t ir_status = getStatus();

  // If the status bit for this rx is set
  if ( ir_status.bits & (1 << which_rx) ) {

    // First, check if there is a message
    // available (+ve non-zero length)
    uint8_t len = getMsgLength( which_rx );

    // valid message len is 1:32. 32 is the
    // maximum number of uint8_ts in an i2c
    // transaction on Arduino
    if ( len > 0 && len < 33 ) {

      ir_mode_t ircomm;

      // Format mode request for which receiver
      if ( which_rx == 0 ) {
        ircomm.mode = MODE_REPORT_MSG0;
      } else if ( which_rx == 1 ) {
        ircomm.mode = MODE_REPORT_MSG1;
      }  else if ( which_rx == 2 ) {
        ircomm.mode = MODE_REPORT_MSG2;
      }  else if ( which_rx == 3 ) {
        ircomm.mode = MODE_REPORT_MSG3;
      } else {
        // error caught above.
      }

      // Set mode to send across the message
      Wire.beginTransmission( IRCOMM_I2C_ADDR );
      Wire.write( (uint8_t*)&ircomm, sizeof( ircomm));
      Wire.endTransmission();

      // Read across uint8_ts using the anticipated len.
      // Store into buffer provided as function argument
      Wire.requestFrom( IRCOMM_I2C_ADDR, len );
      Wire.readBytes( (uint8_t*)buf, len );

      // Let the user know how many bytes were
      // received.
      return (int)len;

    } else {
      // Flag that no bytes were available
      return 0;
    }
  }
  return 0;

}

void SwarmB2_c::printStatus() {
  
  ir_status_t ir_status = getStatus();

  Serial.print("Msg[0:3], Activity[4:7]: ");
  uint8_t mask = 0x01;
  for ( int i = 0; i < 8; i++ ) {
    if ( ir_status.bits & (mask << i) ) {
      Serial.print("1 ");
    } else {
      Serial.print("0 ");
    }
  }
  Serial.println();
}


void SwarmB2_c::printAnyMessage() {

  char buf[32];

  // First, check if any messages are available
  ir_status_t ir_status = getStatus();

  // Message available is first 4 bits
  for( int i = 0; i < 4; i++ ) {
    if ( ir_status.bits & (1 << i) ) {
      memset( (void*)&buf, 0, sizeof(buf) );
      int len = getIRMessage( (uint8_t*)buf, i );
      Serial.print("Rx");
      Serial.print( i );
      Serial.print(" len=");
      Serial.print(len);
      Serial.print(":");
      Serial.print( buf );
      Serial.print(" t=");
      Serial.println( millis ());
    }
  }

  
}

// Queries the IR communication board to see if
// a message has been stored for a receiver.
// There are 4 receivers, [0:3]
// Return:
//  -1    Invalid receiver request
//   0    No message available
//  [0:32]Available message length
uint8_t SwarmB2_c::getMsgLength( int which_rx ) {

  ir_mode_t ircomm;

  if ( which_rx == 0 ) {
    ircomm.mode = MODE_REPORT_LEN_MSG0;
  } else if ( which_rx == 1 ) {
    ircomm.mode = MODE_REPORT_LEN_MSG1;
  } else if ( which_rx == 2 ) {
    ircomm.mode = MODE_REPORT_LEN_MSG2;
  } else if ( which_rx == 3 ) {
    ircomm.mode = MODE_REPORT_LEN_MSG3;
  } else {
    // Invalid receiver
    return -1;
  }

  // Set mode to read back how many uint8_ts are
  // available.
  Wire.beginTransmission( IRCOMM_I2C_ADDR );
  Wire.write( (uint8_t*)&ircomm, sizeof( ircomm));
  Wire.endTransmission();

  // We'll use this struct to check how many
  // uint8_ts are available of a message.
  // 0 uint8_ts means no message.
  ir_msg_len_t msg_len;

  // Request the message size to be sent across into
  // msg_status
  Wire.requestFrom( IRCOMM_I2C_ADDR, sizeof( msg_len ));
  Wire.readBytes( (uint8_t*)&msg_len, sizeof( msg_len ));

  return msg_len.n_bytes;// 0 = error, else [1 : 32]
}
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

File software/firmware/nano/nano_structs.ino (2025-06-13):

/*



*/


#include <avr/io.h>
#include <Wire.h>
#include "ircomm.h"
#include "ircomm_i2c.h"


// Test/Debug modes
#define TEST_DISABLED 0
#define TEST_TX 1
#define TEST_RX 2


#define SELF_TEST_MODE TEST_DISABLED
//#define SELF_TEST_MODE TEST_TX
//#define SELF_TEST_MODE TEST_RX

// A timestamp used only to configure various
// testing/debugging activities.
unsigned long test_ts;
#define TEST_MS 50 // Good for test tx
#define TEST_MS 1000 // good for test rx

// Pin definitions for extra sensors
// on the communication board, if present
#define LDR0_PIN  A0
#define LDR1_PIN  A1
#define LDR2_PIN  A2
#define PROX0_PIN A6
#define PROX1_PIN A7

// Used to control the IR communication.
IRComm_c ircomm;

// Used to track requests made to
// the board over i2c
volatile i2c_mode_t last_mode;
volatile i2c_status_t status;

volatile boolean full_reset;

// Function to receive commands from the master device.
// This will typically be in the format of a mode change
// and then any appropriate data.
void i2c_receive( int len ) {


  // Mode changes are always 1 byte long.  We use these to
  // ready the board to send back information or to ask the
  // board to complete specific actions (e.g, delete a
  // message).
  if ( len == 1 ) { // receiving a mode change.
    i2c_mode_t new_mode;
    Wire.readBytes( (byte*)&new_mode, sizeof( new_mode ) );


    // Check we are setting to a valid mode.
    if ( new_mode.mode < MAX_MODE && new_mode.mode >= 0 ) {
      last_mode.mode = new_mode.mode;
    }

    // For instant mode changes
    // Should we set a last_mode state after this?
    if ( new_mode.mode == MODE_STOP_TX ) {

      // Clearing tx  buff will stop transmission of messages
      ircomm.clearTxBuf();

    } else if ( new_mode.mode == MODE_RESET_STATUS ) {
      full_reset = true;
    } else if( new_mode.mode == MODE_STOP_RX ) {
      ircomm.disabled = true;
      
    } else if( new_mode.mode == MODE_START_RX ) {
      
      ircomm.disabled = false;
      
    } else if ( new_mode.mode == MODE_CLEAR_MSG0 ) {
      // Delete message
      ircomm.clearRxMsg( 0 );


    } else if ( new_mode.mode == MODE_CLEAR_MSG1 ) {
      // Delete message
      ircomm.clearRxMsg( 1 );

    } else if ( new_mode.mode == MODE_CLEAR_MSG2 ) {
      // Delete message
      ircomm.clearRxMsg( 2 );

    } else if ( new_mode.mode == MODE_CLEAR_MSG3 ) {
      // Delete message
      ircomm.clearRxMsg( 3 );


    } else if ( new_mode.mode == MODE_CLEAR_HIST ) {
      ircomm.hist[0] = 0;
      ircomm.hist[1] = 0;
      ircomm.hist[2] = 0;
      ircomm.hist[3] = 0;
    }


  } else { // Receiving a new message to transmit.

    char buf[MAX_MSG]; // temp buffer
    memset(buf, 0, sizeof(buf));
    int count = 0;
    while ( Wire.available() && count < MAX_MSG ) {
      char c = Wire.read();
      buf[count] = c;
      count++;
    }

    // If it is a malformed message from the robot,
    // or the ! symbol
    // we clear the tx_buf and so stop sending messages
    if ( count < 1 ) {
      //Serial.println(" Cleared");

      // CLEAR TX BUF, DISABLE TX
      //memset( tx_buf, 0, sizeof( tx_buf ) );
      ircomm.clearTxBuf();
    } else {
      
      ircomm.tx_len = count;
      //Serial.print("I2C Received:" );
      //Serial.println(buf);
      ircomm.formatString( buf, count );
    }
  }

}

// When the 3Pi or Core2 calls an i2c request, this function
// is executed.
void i2c_request() {

  if ( last_mode.mode == MODE_REPORT_STATUS ) {


    for ( int i = 0; i < 4; i++ ) {
      status.pass_count[ i ] = (uint16_t)ircomm.pass_count[i];
      status.fail_count[ i ] = (uint16_t)ircomm.fail_count[i];
      status.activity[i] = (uint16_t)ircomm.activity[i];
    }

    Wire.write( (byte*)&status, sizeof( status ) );

    //
    // Below are request for message size from the
    // master device.
    //
  } else if ( last_mode.mode == MODE_REPORT_TIMINGS ) {

    i2c_msg_timings_t msg_timings;
    for ( int i = 0; i < 4; i++ ) {
      msg_timings.msg_dt[i] = (uint16_t)ircomm.msg_dt[i];
      msg_timings.msg_t[i] = (uint16_t)ircomm.msg_t[i];
    }
    msg_timings.rx_timeout = (uint16_t)ircomm.ir_config.rx_timeout;
    msg_timings.tx_period = (uint16_t)ircomm.ir_config.tx_period;
    Wire.write( (byte*)&msg_timings, sizeof( msg_timings ) );

  }  else if ( last_mode.mode == MODE_SIZE_MSG0 ) {

    i2c_mode_t msg_status;
    msg_status.mode = ircomm.msg_len[0];
    Wire.write( (byte*)&msg_status, sizeof( msg_status ) );


  } else if ( last_mode.mode == MODE_SIZE_MSG1 ) {
    i2c_mode_t msg_status;
    msg_status.mode = ircomm.msg_len[1];
    Wire.write( (byte*)&msg_status, sizeof( msg_status ) );


  } else if ( last_mode.mode == MODE_SIZE_MSG2 ) {
    i2c_mode_t msg_status;
    msg_status.mode = ircomm.msg_len[2];
    Wire.write( (byte*)&msg_status, sizeof( msg_status ) );


  } else if ( last_mode.mode == MODE_SIZE_MSG3 ) {
    i2c_mode_t msg_status;
    msg_status.mode = ircomm.msg_len[3];
    Wire.write( (byte*)&msg_status, sizeof( msg_status ) );


    //
    // Below are requests for actual message to be
    // reported to the master device
    //
  } else if ( last_mode.mode == MODE_REPORT_MSG0 ) {
    if ( ircomm.msg_len[0] == 0 ) {
      Wire.write("!");  // Error token
    } else {
      Wire.write( ircomm.i2c_msg[0], ircomm.msg_len[0] );
      // Delete message
      ircomm.clearRxMsg( 0 );
    }

  } else if ( last_mode.mode == MODE_REPORT_MSG1 ) {
    if ( ircomm.msg_len[1] == 0 ) {
      Wire.write("!");
    } else {
      Wire.write( ircomm.i2c_msg[1], ircomm.msg_len[1] );
      // Delete message
      ircomm.clearRxMsg( 1 );
    }

  } else if ( last_mode.mode == MODE_REPORT_MSG2 ) {
    if ( ircomm.msg_len[2] == 0 ) {
      Wire.write("!");
    } else {
      Wire.write( ircomm.i2c_msg[2], ircomm.msg_len[2] );

      // Delete message
      ircomm.clearRxMsg( 2 );
    }


  } else if ( last_mode.mode == MODE_REPORT_MSG3 ) {
    if ( ircomm.msg_len[3] == 0 ) {
      Wire.write("!");
    } else {
      Wire.write( ircomm.i2c_msg[3], ircomm.msg_len[3] );

      // Delete message
      ircomm.clearRxMsg( 3 );
    }
    
  } else if ( last_mode.mode == MODE_REPORT_CYCLES ) {
    i2c_cycles_t cycles;
    cycles.tx_count = ircomm.tx_count;
    cycles.rx_cycles = ircomm.rx_cycles;

    // Transmit
    Wire.write( (byte*)&cycles, sizeof( cycles ) );

  } else if ( last_mode.mode == MODE_REPORT_ERRORS ) {
    i2c_errors_t errors;

    for ( int i = 0; i < 4; i++ ) {
      for ( int j = 0; j < 4; j++ ) {
        errors.error_type[i][j] = ircomm.error_type[i][j];
      }
    }

    // Transmit
    Wire.write( (byte*)&errors, sizeof( errors ) );

  } else if ( last_mode.mode == MODE_REPORT_RX_ACTIVITY ) {
    i2c_activity_t activity;
    for ( int i = 0; i < 4; i++ ) {
      activity.rx[i] = ircomm.rx_activity[i];
    }
    // Transmit
    Wire.write( (byte*)&activity, sizeof( activity ) );

  } else if (  last_mode.mode == MODE_REPORT_RX_DIRECTION ) {

    i2c_bearing_t bearing;
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

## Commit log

2024-06-20 significant changes to nano firmware
    [swarm_b2_bom.xlsx]
2025-12-03 Implemented an escape routine for the start byte, need to put back the tracking of rx errors for metrics
    [config.h, ir_parser.cpp, ir_parser.h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]
2025-12-23 Big restructuring. Implementing Arduino master side class
2025-12-27 moved nano-neo from timer2 to timer1. Need to do the same with nano
2026-03-01 Revise README for SwarmB2 with features and usage
    Updated README with detailed features, usage instructions, and important considerations for the SwarmB2 IR Communication board.
2026-03-01 Document future improvements for the board design
    Added section on improvements for future revisions of the board, including suggestions for additional features and hardware changes.
2026-03-27 Potential bug fix in ircomm.cpp, line 670
    [ircomm.cpp, ircomm_i2c.h]
2026-04-17 I think disableRx had a bug where the serial object buffer was not flushed. I've stripped out more parameters in an attmept to simplify things.
    [SwarmB2.cpp, config.h, ir_parser.cpp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]
2026-04-19 add a new 1 byte message status feature so that the board can be polled quickly.
2026-04-21 removed NeoHWSerial from the project. I'll investigate frame errors on the SwarmB3 board instead
    [config.h, ir_parser.cpp, ir_parser.h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]
2026-04-24 Found a bug in the parser class where it wasn't reporting one byte received if the byte received was just an intermediate byte in the paylod. That would have been effecting the activity log, and the 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
    [M5SlaveDisplay.ino, M5Visualiser.ino, M5_IRComm_RxTest.ino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]
2026-05-07 updated parser class to return a struct, which simplifies the update() in ircomm. Updated bearing to resolve against the theoretic max bytes that can be received, so the vectors will contain a value 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
    [ir_parser.cpp, ir_parser.h, ircomm.cpp]
2026-05-18 Enhance README with configuration and usage info
    Updated README to include additional configuration details and usage instructions for the Swarm-B2 board.
